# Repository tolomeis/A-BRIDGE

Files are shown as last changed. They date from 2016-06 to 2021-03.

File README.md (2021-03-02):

View this project on [CADLAB.io](https://cadlab.io/project/1067). 

# A-BRIDGE
Source files for the A-BRIDGE motor driver board

The A-Bridge is a small dual H-BRIDGE based on the integrated DMOS full-bridge A4950, capable to run 2 motors with a continuos current of 3A (3.5 with a heat dissipator) and a peak current of 5A. The bridge operates in PWM LAP, so, compared to the typical PWM SM control, you have less resolution but a more precise control of the speed. The inverted PWM signal required for LAP control is generated internally with a 74HC240 tri-state inverter, that also gives you the possibility to disable the bridge and the motor using the Enable input.

FEATURES:
 + Control 2 brushed DC motors
 + Input voltage: 8-40V
 + Output current: 3A continuos, 3.5 with heat dissipator, 5A peak
 + Overcurrent  short circuit protection
 + Enable input to disable the bridge

WARNING:
Some motor manifacturers (e.g. micromotors) use capacitors to reduce spikes and noise, it's recommended not to use that type of motors with this bridge. Check the motor's specification to know if your motor has the capacitors.
 
---

How to use

Basically this is a H Bridge, the only difference between this and the other typical commercial bridges is the integrated LAP control, this mean that you can control both speed and direction using the same signal. In particular:

|PWM duty cycle  |Motor speed|
|---|---|
|0% |Full Backwards|
|50% |Brake |
|100% | Full Forwards|

The ENABLE pin is used to disable the bridge. When LOW the bridge is operating at normal condition, when HIGH the bridge will enter in low power standby mode after 1ms. This is useful because the *brake* condition, with duty cycle 50%, does not means that the motor is turned off, but means that the motor is **braked, and it will draw current to remain still**. This is the worst efficience condition for the bridge, then, unless with small motor, it will heat up very fast. I recommend you not to remain in *brake* conditon for more than a half a minute. Therefore, for simply stop the motor you can set duty cicle to 50% and then disable the bridge with EN pin.

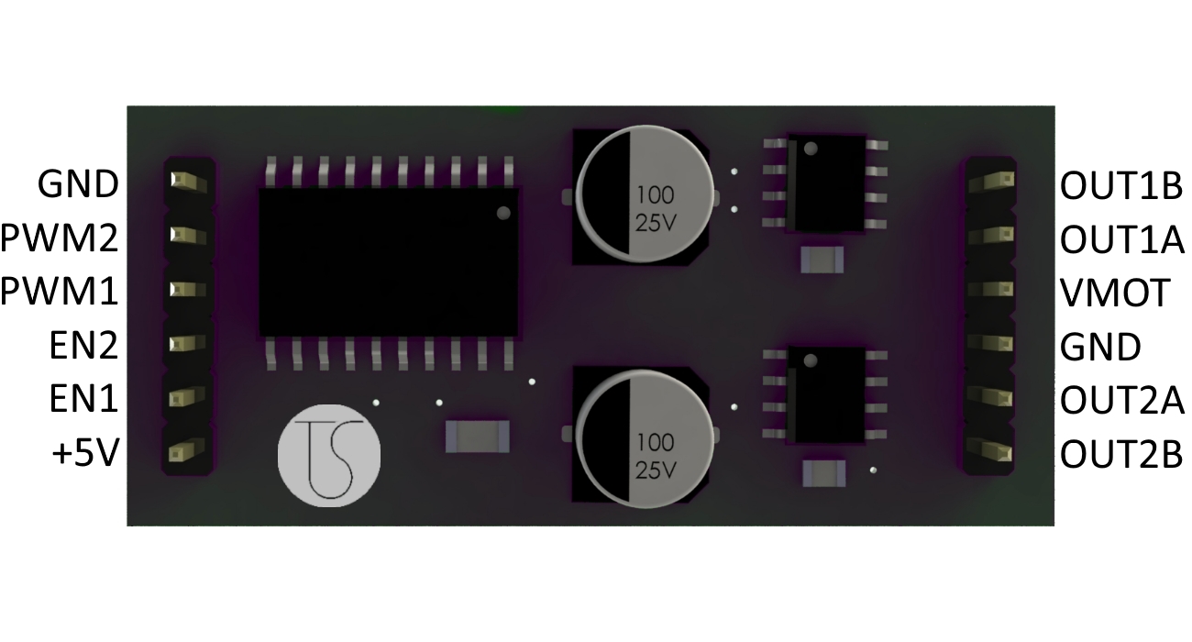
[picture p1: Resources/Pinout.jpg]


------

The circuit is very simple, basically it consist of two A4950, the 74HC240 and 5 bulk capacitors.

The A4950 can also provide a current feedback, but the  sensing resistor also triggers the automatic current limiting system of the IC, that decrease the maximum output current. For example, a 0.25ohm resistor would limit the maximum current to 2A. This is the reason why i choose not to use the current sensing in this version of the board. If you want the current sensing feature you can use a external ammeter IC or consider the powerful [uBridge by Officine Robotiche](https://github.com/officinerobotiche/uBridgePCB).

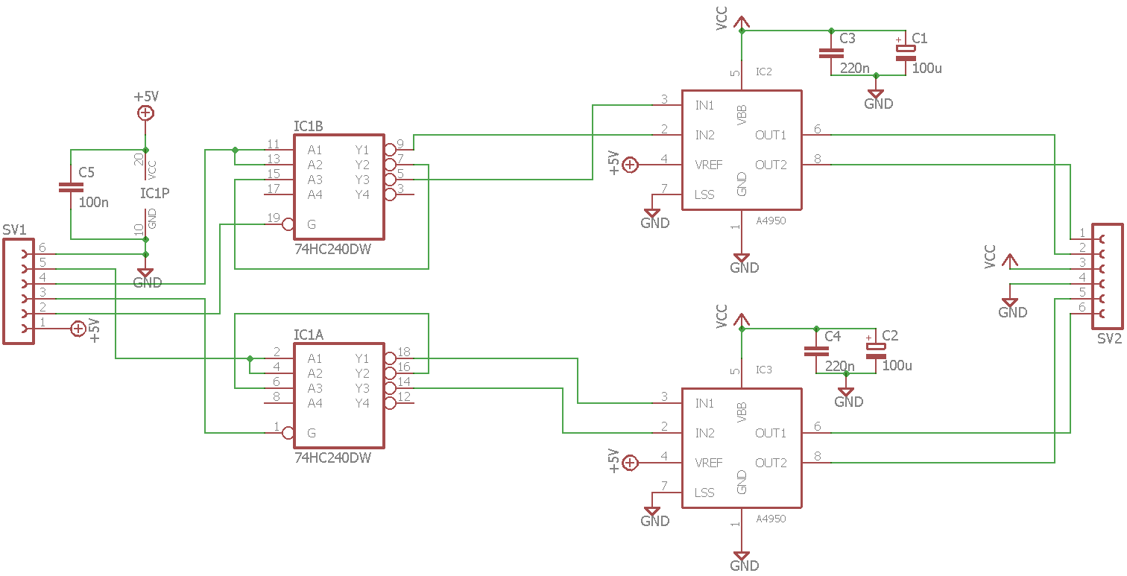
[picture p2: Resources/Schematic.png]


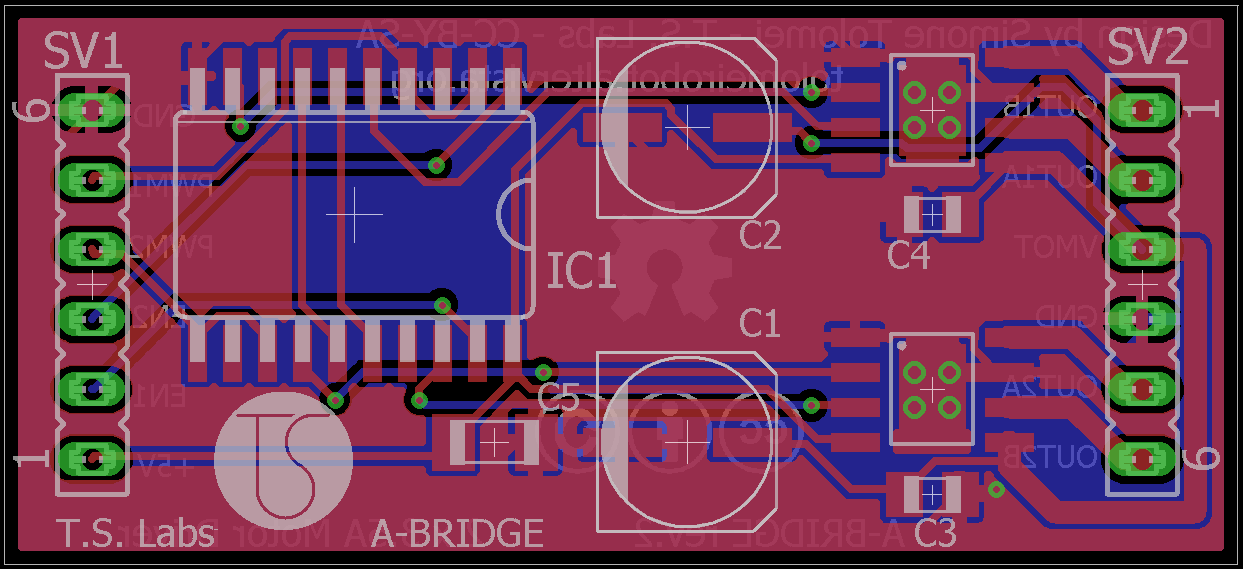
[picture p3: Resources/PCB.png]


----

###TESTING

Every bridge is tested with various conditions of load. The tests measures voltage drop, voltage overshoot, rise time and temperature.
Here you can see differents measures obtained with 2 different motors: a micromotors 12V 300mA geared motor and a lawnmower motor, running at 20V and absorbing 600mA with no load. You can see that with the lawnmower robot motor the voltage overshoot is really high, this happens mainly because the Arduino (which i used in this tests) produces the PWM signal with a too low frequency, 1Khz or 5Khz depending by the pin. To use big motors i recommend to use a frequency PWM at least of 10-15Khz, for example by using the [setPwmFrequency](http://playground.arduino.cc/Code/PwmFrequency) function on Arduino or by using another microcontroller (e.g. ARM or PIC)

###Micromotors motor:

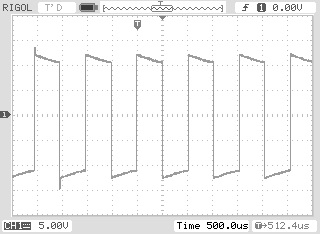
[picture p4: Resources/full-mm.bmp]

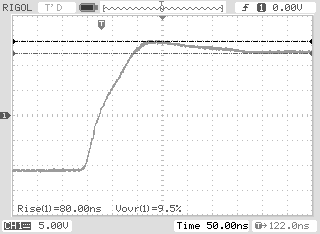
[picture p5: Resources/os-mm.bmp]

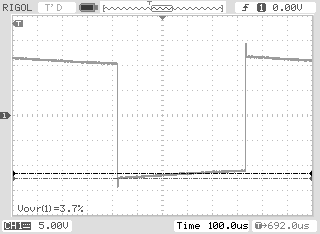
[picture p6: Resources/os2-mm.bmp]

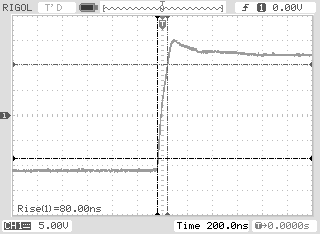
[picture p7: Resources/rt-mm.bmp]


###Lawnmower motror:

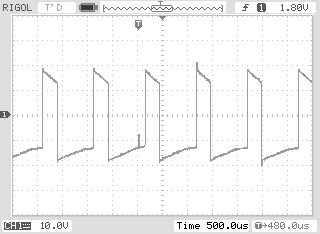
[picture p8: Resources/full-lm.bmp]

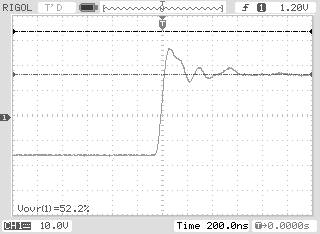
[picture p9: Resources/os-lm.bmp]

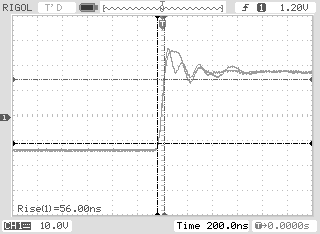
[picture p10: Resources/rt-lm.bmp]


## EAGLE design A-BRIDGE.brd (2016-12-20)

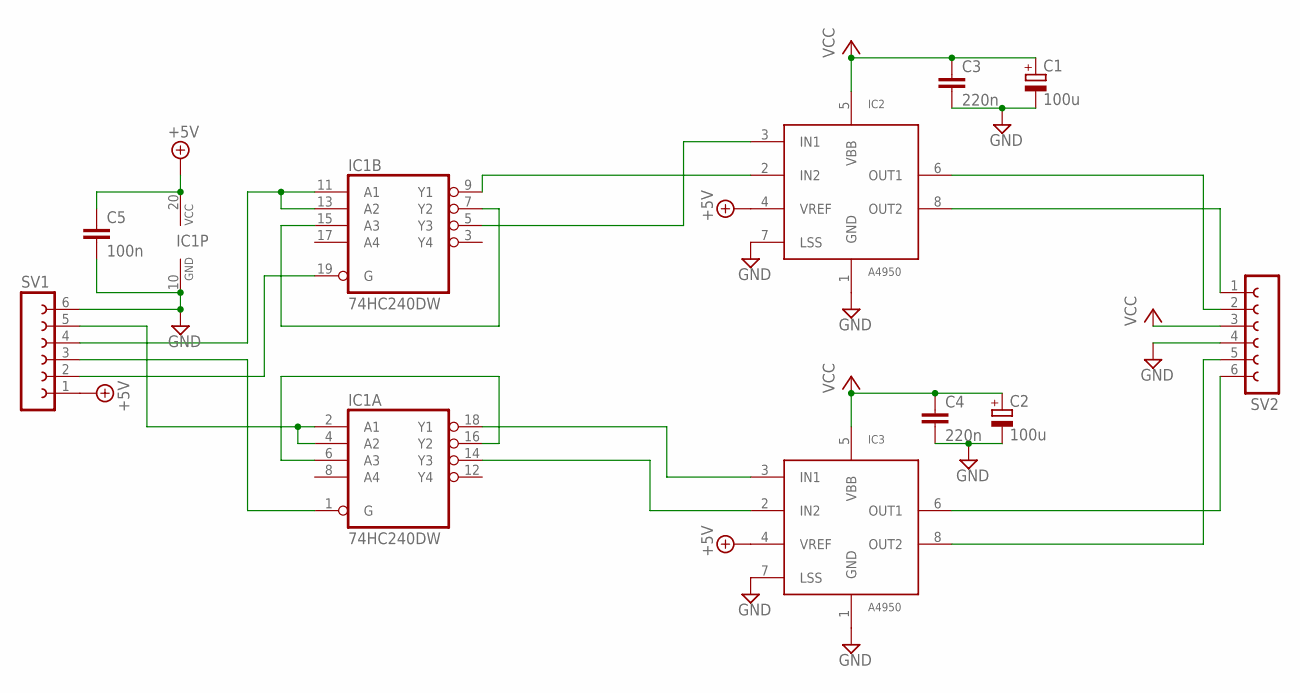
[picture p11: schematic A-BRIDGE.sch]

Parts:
C1, C2: 100u; UD-6,3X7,7_NICHICON_HS
C3, C4: 220n; C0805K
C5: 100n; C1206K
IC1: 74HC240DW; SO20W
IC2, IC3: A4950; SOICN-8
SV1, SV2: FE06-1; FE06

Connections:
+5V: C5.1, IC1.20 (VCC), IC2.4 (VREF), IC3.4 (VREF), SV1.1
GND: C1.-, C2.-, C3.2, C4.2, C5.2, IC1.10 (GND), IC2.1 (GND), IC2.7 (LSS), IC3.1 (GND), IC3.7 (LSS), SV1.6, SV2.4
unnamed: IC2.6 (OUT1), SV2.2
unnamed: IC2.8 (OUT2), SV2.1
unnamed: IC3.6 (OUT1), SV2.6
unnamed: IC3.8 (OUT2), SV2.5
unnamed: IC1.14 (Y3), IC3.2 (IN2)
unnamed: IC1.18 (Y1), IC3.3 (IN1)
unnamed: IC1.6 (A3), IC1.16 (Y2)
unnamed: IC1.2 (A1), IC1.4 (A2), SV1.5
unnamed: IC1.11 (A1), IC1.13 (A2), SV1.4
unnamed: IC1.7 (Y2), IC1.15 (A3)
unnamed: IC1.9 (Y1), IC2.2 (IN2)
unnamed: IC1.5 (Y3), IC2.3 (IN1)
unnamed: IC1.1 (G), SV1.3
unnamed: IC1.19 (G), SV1.2
VCC: C1.+, C2.+, C3.1, C4.1, IC2.5 (VBB), IC3.5 (VBB), SV2.3

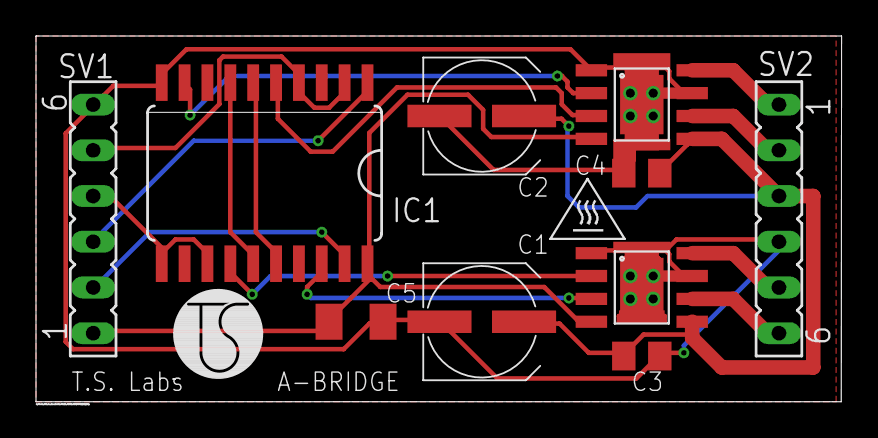
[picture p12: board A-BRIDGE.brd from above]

Board: 2 copper layers, 44.8 x 20.3 mm, 10 parts (0 on the bottom side), 17 nets.

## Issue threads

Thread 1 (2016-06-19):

Electrolytic capacitors footprint too small for hand soldering

tolomeis, 2016-06-19:

Closed 2016-12-20.

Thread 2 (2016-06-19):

Missing pinout on silkscreen

tolomeis, 2016-06-19:

tolomeis, 2016-09-28:
Added in rev. 2

Closed 2016-09-28.

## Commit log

2016-06-18 Added first files
    [A-BRIDGE.brd, A-BRIDGE.sch]
2016-09-24 A-BRIDGE rev.2
    Added silkscreen pinout
    Fixed grounding problems
    Better Heat dissipation
    [A-BRIDGE.brd]
2016-12-20 rev2.01
    Added "hot surface" warning
    Better heat dissipation on bottom area
    Bigger capacitor's footprint for hand soldering
    [A-BRIDGE.brd, A-BRIDGE.sch]

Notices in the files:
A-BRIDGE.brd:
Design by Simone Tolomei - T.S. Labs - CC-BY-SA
